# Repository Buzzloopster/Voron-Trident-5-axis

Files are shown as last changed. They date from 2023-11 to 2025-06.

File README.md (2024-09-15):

# Voron-Trident-5-axis
This is an 5 axis modification of Voron Trident 250mm 

Printer parameters:

CoreXYAC

Axis X and Y travel limits +110mm and -110mm from rotary bed centre

Axis Z travel limits Z + 130mm and Z -45mm 

Axis A can swivel 110 degrees in both directions

Axis C can turn infinite 

You can find two different versions of the Z-axis mechanism

DIRECT DRIVE EXTRUDER with OMG extruder

and

BOWDEN DRIVE EXTRUDER mounted at the back of the printer

https://youtube.com/@loopster77?si=zdEiBNTgb2wkNzhc

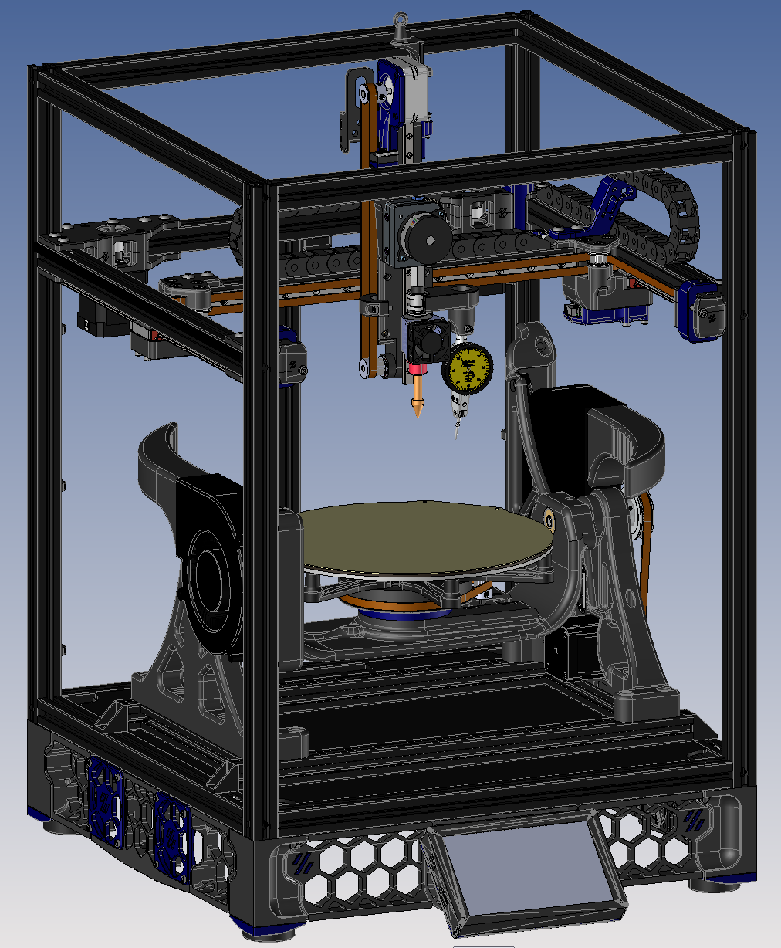
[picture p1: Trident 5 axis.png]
Trident 5 axis


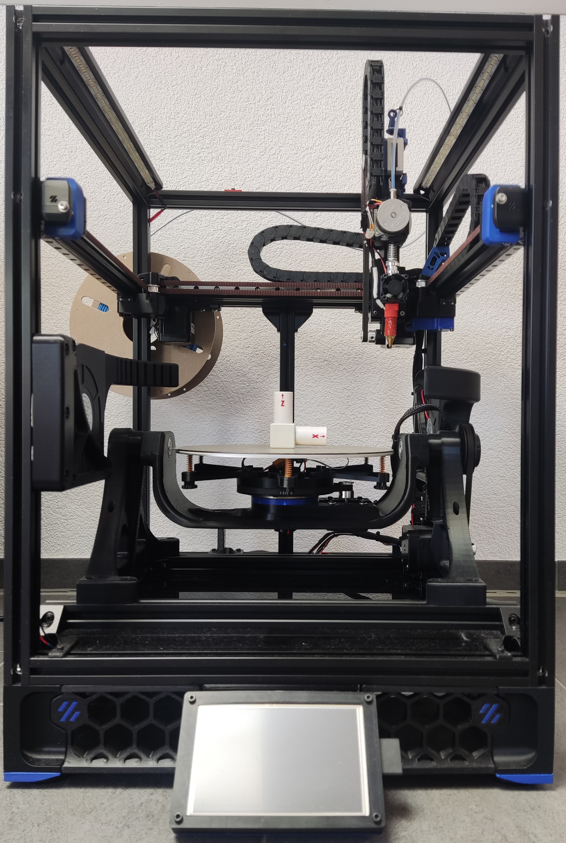
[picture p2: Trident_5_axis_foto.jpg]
Trident_ 5_axis_foto_1


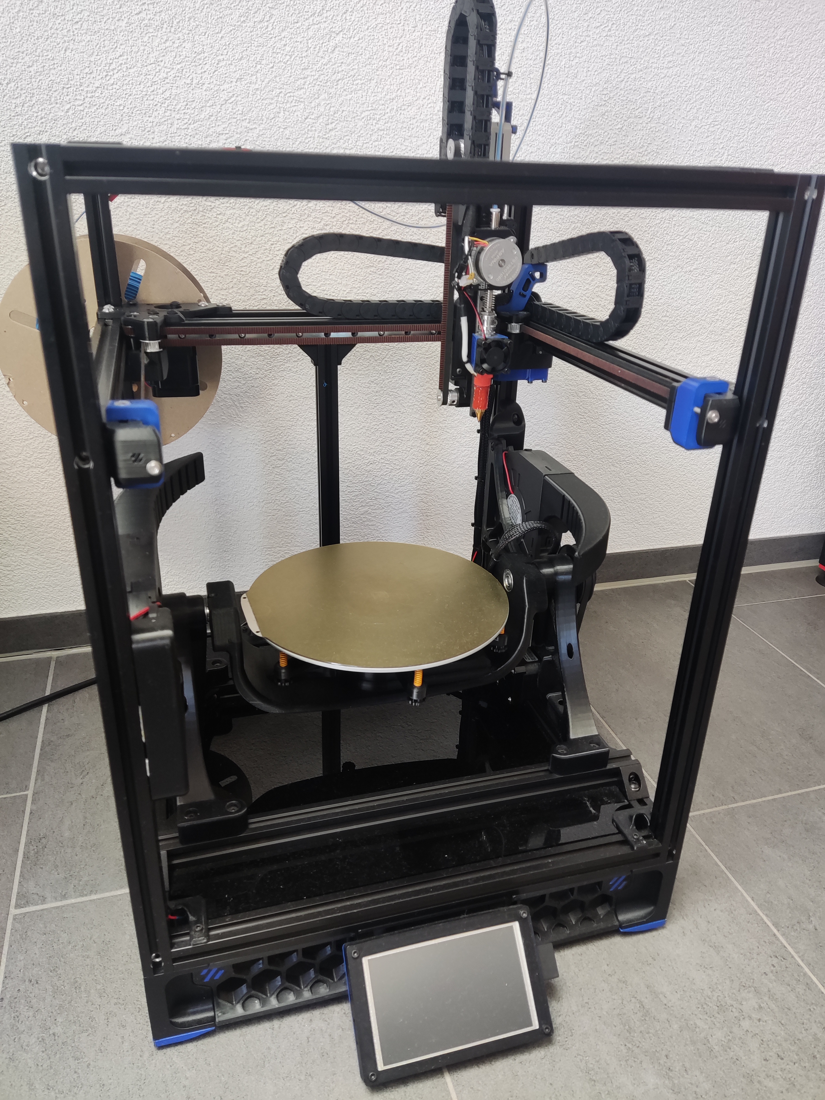
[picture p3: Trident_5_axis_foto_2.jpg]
Trident_ 5_axis_foto_2


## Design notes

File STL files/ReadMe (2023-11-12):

ALL PARTS ARE DESIGNED TO BE PRINTED WITH ABS FILAMENT! ! !

YOU CAN USE THIS SETTINGS FOR SLICING AND PRINTING THIS PARTS 

Layer height: 0.2mm
Extrusion width: 0.4mm, forced
Infill pecentage: 50%
Infill type:  gyroid, honeycomb, triangle, or cubic
Wall count: 5
Solid top/bottom layers: 5

NO WARPING!

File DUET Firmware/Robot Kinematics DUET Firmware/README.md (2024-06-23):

# RepRapFirmware_robot
only cpp, h and binaries

based on RRF 3.5.0beta3. To compile, use all related projects which are tagged with this release number.

Changes needed for compilation:
- Config/Pins.h add a SUPPORT_ROBOT flag and set to 1
- set other types to 0, for 6HC Hangprinter flag must be set (used for CAN)
- Kinematics.h change robot5axis to robot
- Kinematics.cpp add robot case to initiate the robot Kinematics class
- include RobotKinematics.* into Movement/Kinematics folder

The changed Pins.h, Kinematics.h and .cpp are checked in.

Duet 2 compilation is critical with memory usage, disable all other kinematics in Pins.h to have a chance.

For 6HC, the Hangprinter flag in Pins.h must be set.

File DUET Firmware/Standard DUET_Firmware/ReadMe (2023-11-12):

This is Firmware for Duet 6HC board with settings based on my build. 
For a new build the values of bed center needs to be recalibrated and adjusted to the absolute zero of printer

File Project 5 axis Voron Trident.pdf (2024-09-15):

## Project 5 axis 3D printer Voron Trident

For the project I chosed an 3D printer Voron Trident 250mm from open source, because of the excellent core XY gantry. The rotary bed and the Z axis extruder and hotend are designed as extention modules and can be adapted to any kind of core XY 3D printer. All parts are printed from ABS filament and in the future i would like to make the 3D printer fully enclosed.

Everything was its build, was considered for people on budget and with no access to CNC machines and whole build can be finished with a bit of knowledge of mechanics

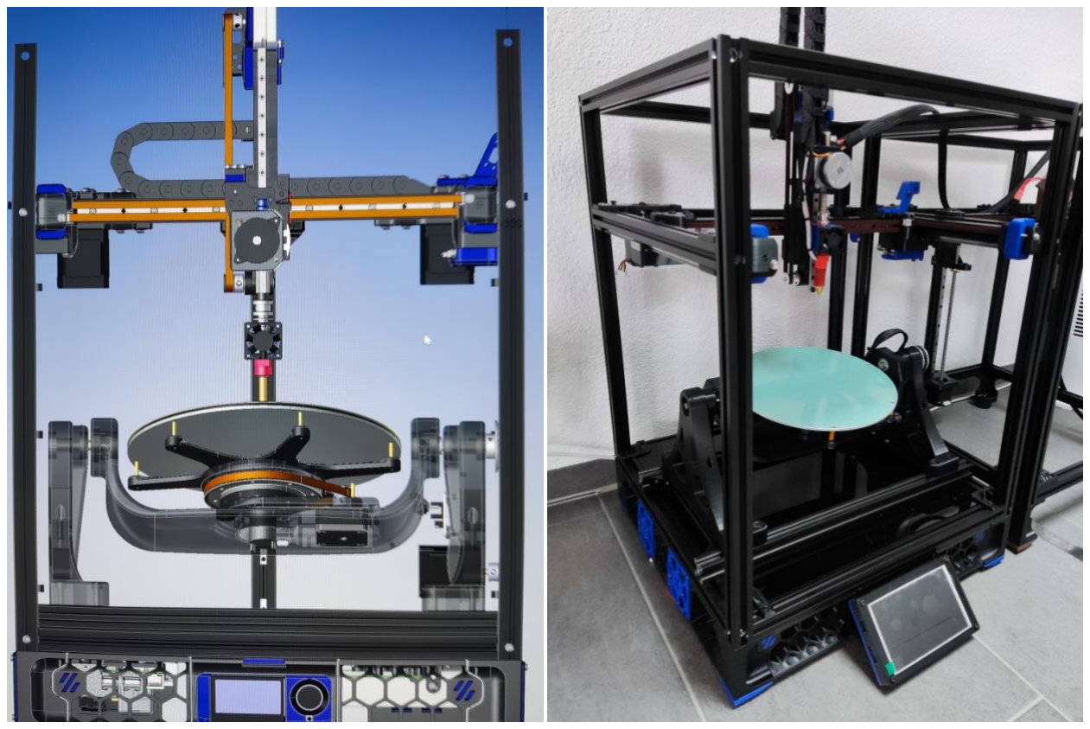
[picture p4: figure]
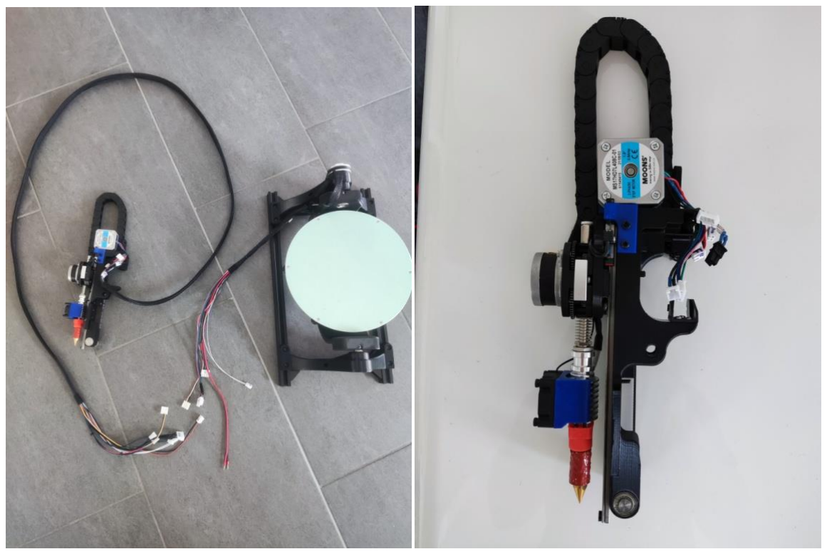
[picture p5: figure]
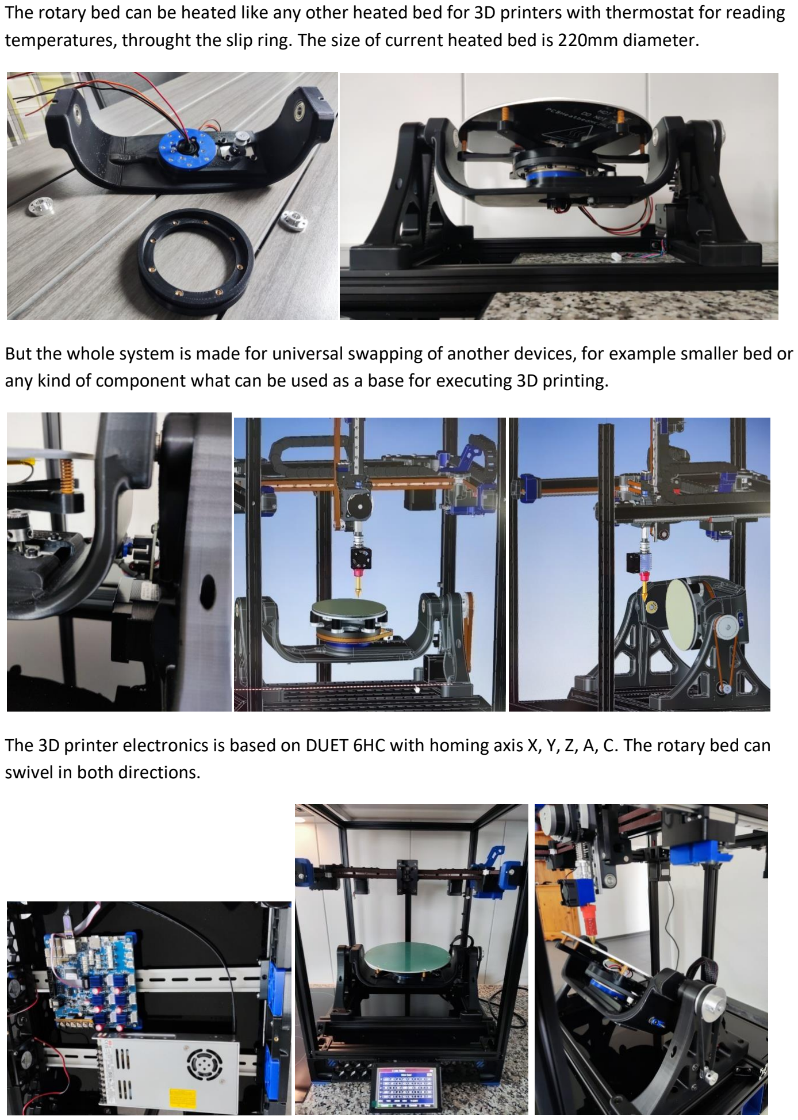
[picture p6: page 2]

The rotary bed can be heated like any other heated bed for 3D printers with thermostat for reading temperatures, throught the slip ring. The size of current heated bed is 220mm diameter.

But the whole system is made for universal swapping of another devices, for example smaller bed or any kind of component what can be used as a base for executing 3D printing.

The 3D printer electronics is based on DUET 6HC with homing axis X, Y, Z, A, C. The rotary bed can swivel in both directions.

The 3D printer is already build and tested only with standard slicers such as Prusa slicer or Super slicer. I have made indicator clock device to adjust the printer to the tight tolerances. The whole motivation behind this project is to bring and educate communities of hobbyists or people interested in additive manufacturing, new way of processing FDM methods to create and produce parts what can eliminate weak characteristics of layer adhesion by combining layer deposition from different angles of produced components.

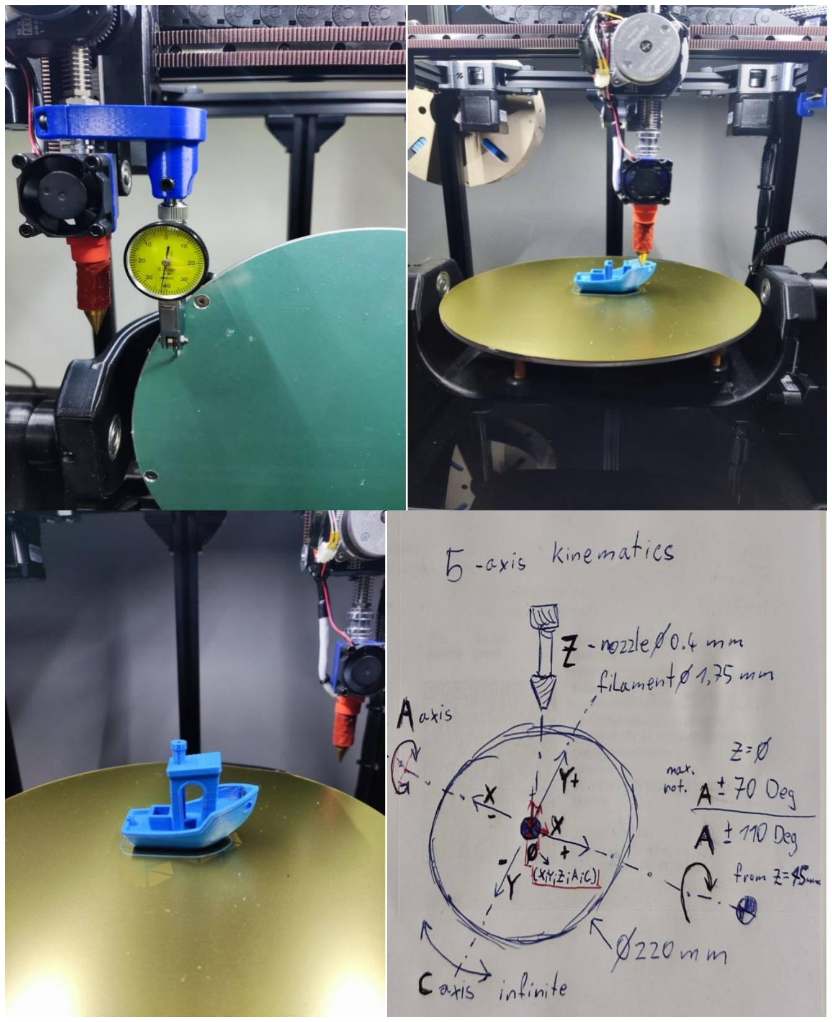
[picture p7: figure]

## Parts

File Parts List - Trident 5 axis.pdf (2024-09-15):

# Base

Aluminium Extrusion 2020 | Lenght 410mm | 2
Aluminium Extrusion 2020 | Lenght 180mm | 2
90 Degree corners | For Aluminium profile 2020 12
Screw | M5 x 10mm | 24
Screw | M5 x 20mm | 12
T nuts | M5 | 36
Heat insert | M3 x 5mm | 2
Screw SHCS | M3 x 8mm | 6
High precision Bearing | 608ZZ | 4
Spacer M8 x 1mm | | 2
Spacer M3 x 0.7 mm | | 4
Shaft 8mm Left | lenght 57 mm | 1
Shaft 8mm Right | lenght 79 mm | 1
Nema 17 stepper motor | 48mm 0.9deg, optimal 2.0Amp | 1

optical switch sensor for 3D

Closed loop GT2 belt 6mm | lenght 302 or 303 mm | 1
Pulley GT2 | 80 tooth 8mm bore | 1
Pulley GT2 | 16 tooth 5mm bore | 1
printer | 1

https://www.amazon
.com/MakerHawk-Optical-Endstop-Photoelectric-Control/dp/B07PMW
2QMT/ref=sr_1_1?ke
ywords=Optical+Ends
top&qid=170015654
4&sr=8-1

# Parts list Voron Trident 5-axis

# Table

Heat insert | M3 x 5mm | 52
Screw SHCS | M3 x 8mm | 52
Screw SHCS | M3 x 10mm | 20
Screw SHCS | M3 x 12mm | 1
Screw SHCS | M3 x 20mm | 6
Screw FHCS | M3 x 30mm | 6
Spacer M3 x 0.7 mm | | 7
NEMA_17_20mm 1.8deg | | 1
Pulley GT2 | 20 tooth 5mm bore | 1
Slip Ring | Dia 22mm 4CH 10A | 1

https://www.amazon
.com/s?k=slip+ring+4
+wire&crid=2COT7G
QJ0ZHZ7&sprefix=sli
p+ring+4+wire%2Cap
s%2C217&ref=nb_sb
_noss_1
IGUS ring | PRT_04_30
High precision Bearing | 608ZZ | 2
Closed loop GT2 belt 6mm | lenght 330mm | 1
Pololu Hub 8mm | The six M3 holes needs to be drilled with 3.2mm drill | 2
Round Heated bed round for kossel 220mm 24V | | 1
Round Magnetic sheet 220mm | | 1
Round PEI sheet 220mm | for kossel | 1
Bed spring | ID 3mm OD 6mm Lenght 15mm | 6
Diameter 90mm | 1

https://www.igus.ch/
product/iglidur_PRT_
04?artnr=PRT-04-30

# Z - axis Hotend with Extruder plus touch screen and blower fan

Heat insert | M3 x 5mm | 27
Heat insert | M2 x 4mm | 13
Screw SHCS | M2 x 6mm | 17
Screw SHCS | M3 x 8mm | 18
Screw SHCS | M3 x 10mm | 6
Screw SHCS | M3 x 12mm | 6
Screw SHCS | M3 x 14mm | 8
Screw SHCS | M3 x 16mm | 3
Screw FHCS stainless steel !!! | M3 x 8mm | 4
Screw FHCS | M3 x 22mm | 2
Screw FHCS | M3 x 6mm | 6
Screw BHCS | M5 x 10mm | 8
Screw BHCS | M5 x 25mm | 5
T nuts | M5 | 5
Hex nut | M3 | 4
Spacer M5 x 1mm | | 1
Spacer M2 x 0.5 mm wide | to fit the mouting hole | 4
neodymium magnets | 6 x 3 mm | 4
Self taping Screw | M2 size for micro switch | 2

MGN7 - H Linear Rail | Lenght 200mm | 1
NEMA_17_20mm 1.8deg | can be used from the voron kit | 1
Small Shaft 5mm | Lenght 45mm | 1
Shaft Collar 5mm | | 1
High precision Bearing | 625 ZZ | 2
Pulley GT2 | 20 tooth 5mm bore | 2
GT2 belt 6mm | Lenght 500mm | 1
Micro switch for 3d printer | | 1
Nonplanar nozzle | 0.4mm | 1
24V Ceramic Heating Core | CHC | 1
Heat Break For 1.75mm Filament M6 | for V6 Hotend | 1
Chain link 10x11 | 0.5m | 1
PTFE Tube OD 4mm ID 2.5mm | 1.0 M then cut it tio required lenght | 1
PTFE Tube OD 4mm ID 2.0mm | 200mm then cut it tio required length in between hot end and extruder | 1
24V Blower Fan 120x120x32mm | Printer will be installed with TWO Fans LEFT and RIGHT side | 2
24V Fan 30x30x10mm | | 1
Zip ties | | 100
Indicator Finger Clock for bed and axis calibration | 0.01mm sensitivity | 1

https://www.nonpla
nar.xyz/nozzles

https://imprimante-3dservice.com/gb/553-
trianglelab-chc-v6-
24v-115w-ceramicheater.html

https://en.wikipedia.
org/wiki/Indicator_(d
istance_amplifying_i
nstrument)

https://rdbarrett.co.uk/product/dial-test-indicatorhorizontal-type-08mm-001mm-mitutoyo-fingerclock/

## This parts are only for, if you decide to build Direct Drive version

DM1 OMG V2S Extruder kit with stepper motor and M6 to M10 adapter | with M6 to M10 adapter and stepper motor | 1
V6 HeatSink Extruder Radiator 3D Printer | bottom, top 1/8 or M10mm thread | 1

https://www.omgext
rd.com/productpage/omgextrd-omg-

https://store.dremc.com.a
u/products/omg-v2s-allmetal-direct-extruder-

# Z - axis Hotend with Extruder plus touch screen and blower fan

## This parts are only for, if you decide to build Bowden Drive version

PTFE Tube OD 4mm ID 2.0mm | 1M then cut it tio required length in between hot end and extruder | 1
V6 pro adapter in between nozzle and heat element CHC | M6 thread | 1
Phaetus x Voron Dragon Standard Flow or Highflow Hotend | | 1

https://meltbro.de/v
6-pro-adapterersetzt-volcanohotend-fuer-v6-
nozzle-duese-ausvernickeltem-

https://3do.eu/spareparts/672-v6-pro-adapterto-increase-super-flow-ofv6-rapidohot-end.html

https://www.3dmens
ionals.de/phaetus-xvoron-dragonhotend-st-2069#attr=9949,995
1,22290

https://www.phaetus.com
/products/phaetus-xvoron-hotend-st

Extruder for 1.75mm filament ( for exmple BondTech) mounted at back of the frame of the printer | BMG mounted with bracket on 2020 aluminium profile near to filamnet spool holder | 1
Pneumatic Coupler PC4-M10 With Collar | PC4 - M10 | 1

https://www.bondte
ch.se/product/bmgextruder/

https://www.whamb
amsystems.com/pro
ducts/metal-couplerpc4-m10

# Controls

Duet 6HC board | | 1
Power supply output 24V | 350W min. | 1
Paneldue touch screen 5" | | 1
Rj-45 cable, 0.5m | male to female | 1
Optional | Raspberry Pi4 | 1

https://www.duet3d.
com/duet3mainboar
d6hc

https://docs.duet3d.
com/Duet3D_hardwa
re/Accessories/Panel
Due

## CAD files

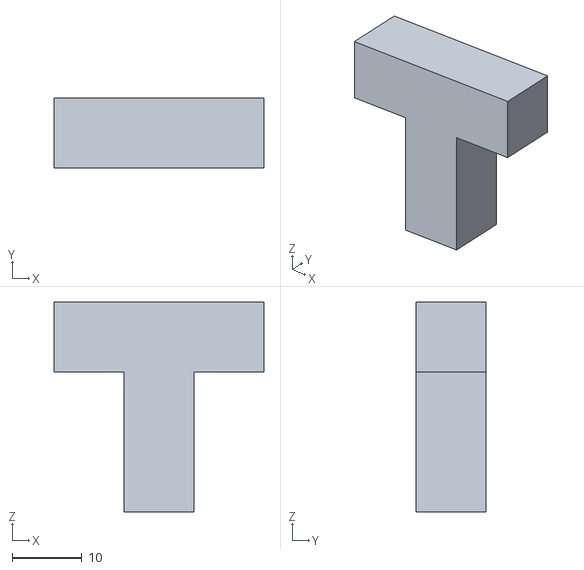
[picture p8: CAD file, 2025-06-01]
Printer Calibrations/T_letter.stl
30.0 x 10.0 x 30.0

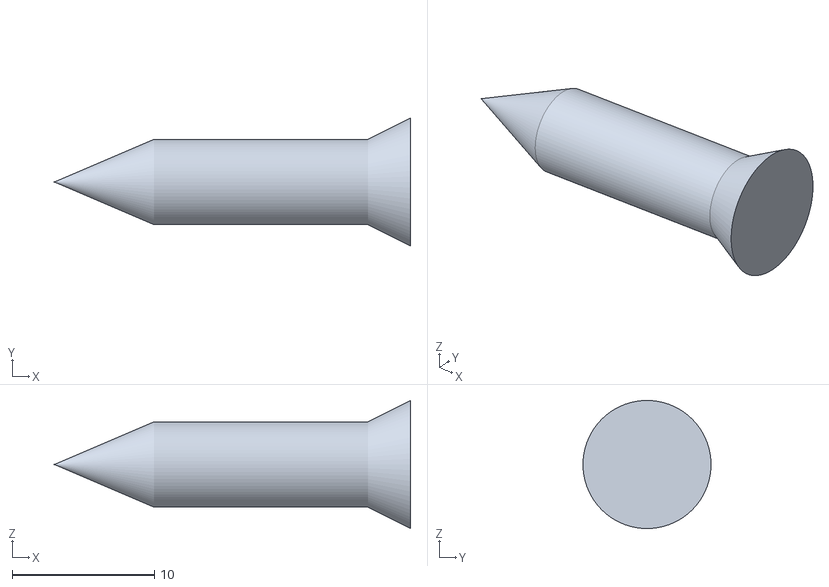
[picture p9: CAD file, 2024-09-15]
STL files/Robot Kinematics testing pin.stl
25.0 x 9.00 x 9.00

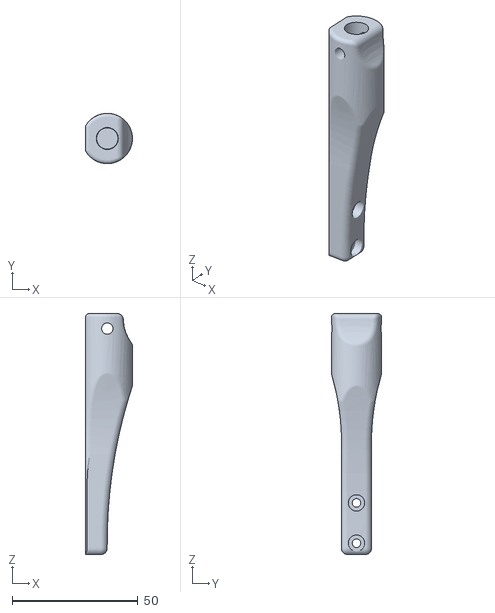
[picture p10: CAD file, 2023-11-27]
STL files/Z-axis Bowden drive - Dragon Hotend for Voron/indicator clock holder - Bowden drive.stl
18.7 x 20.0 x 95.8

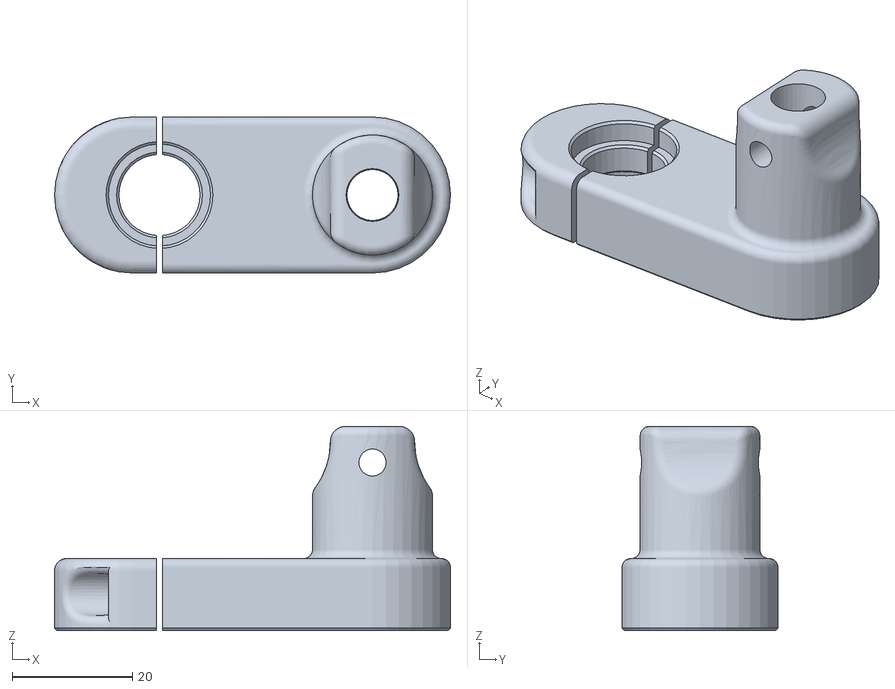
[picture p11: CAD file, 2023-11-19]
STL files/Z-axis Direct drive/indicator clock holder.stl
66.0 x 26.0 x 34.0

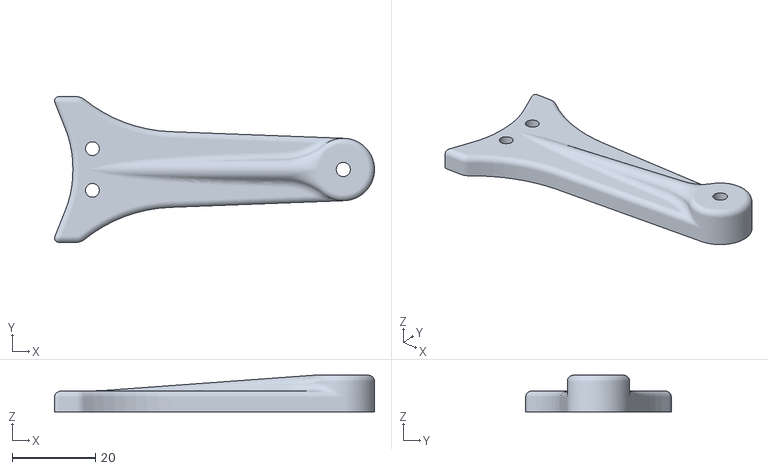
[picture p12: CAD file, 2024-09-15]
STL files/rotary table pivot ver 0.2.stl
76.9 x 35.0 x 8.80

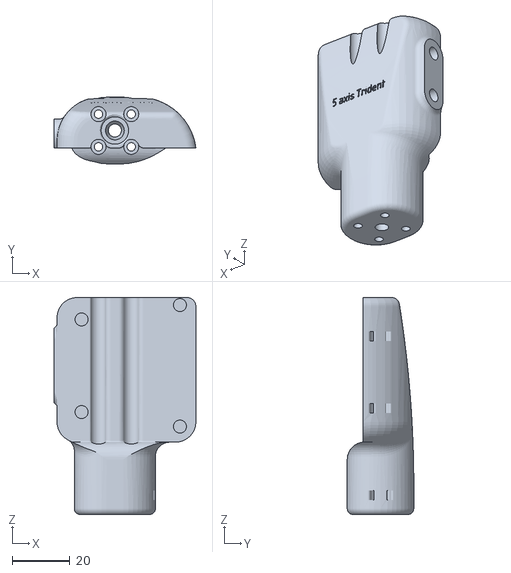
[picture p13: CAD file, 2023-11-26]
STL files/Z-axis Bowden drive - Dragon Hotend for Voron/Z-axis hotend holder.stl
49.0 x 23.0 x 75.0

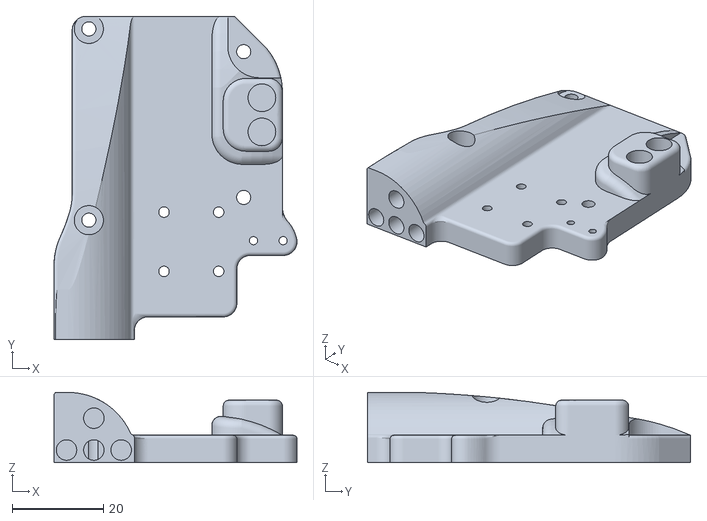
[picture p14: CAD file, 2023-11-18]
STL files/Z-axis Direct drive/Extruder_linerar_rail_mount.stl
53.4 x 71.0 x 15.4

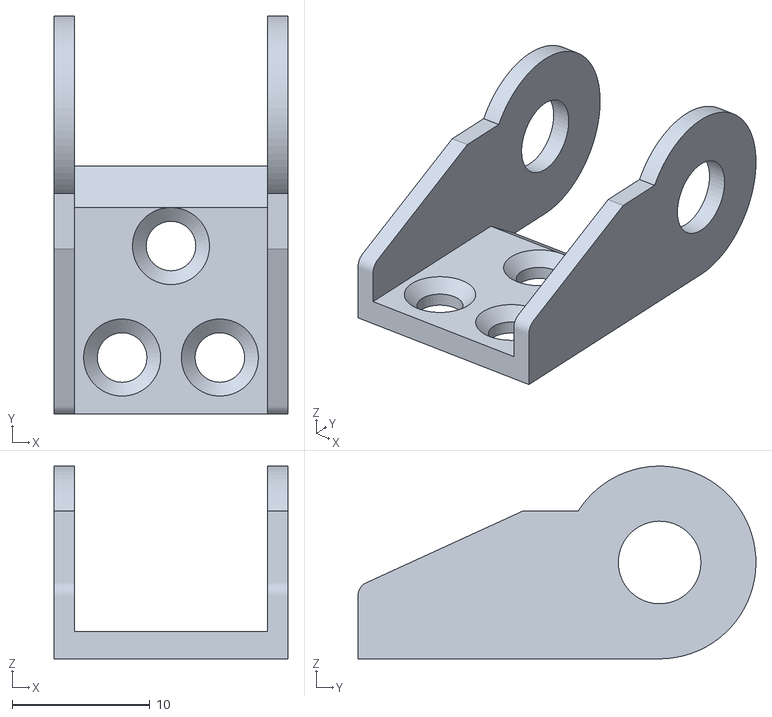
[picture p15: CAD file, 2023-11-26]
STL files/10x11-chain-edge2.stl
17.0 x 28.9 x 14.0

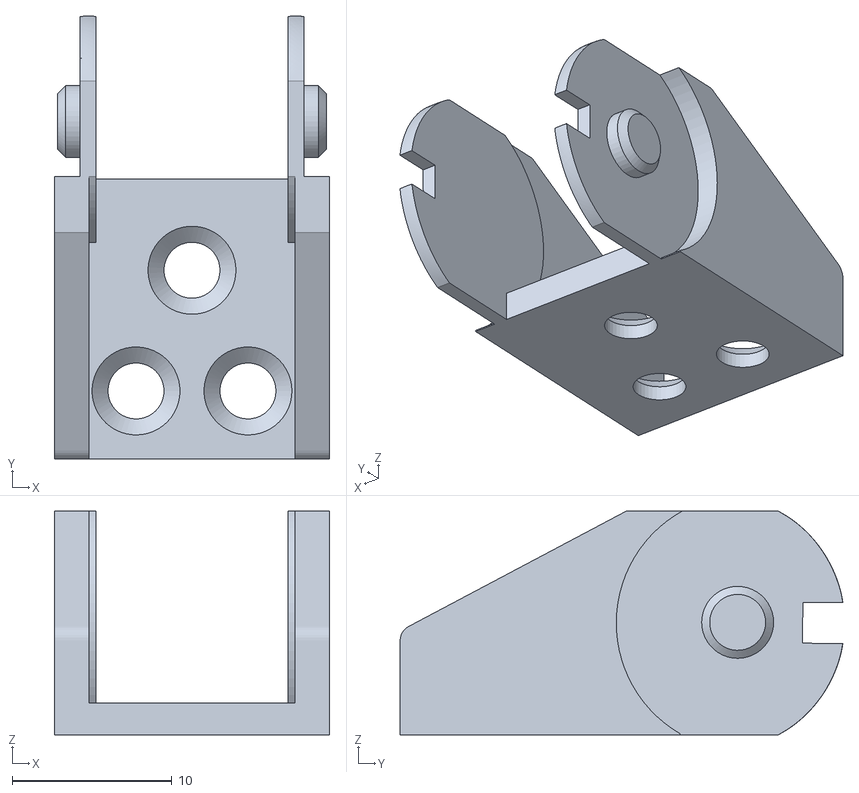
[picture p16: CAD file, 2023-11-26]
STL files/10x11-chain-edge1.stl
17.2 x 27.7 x 14.0

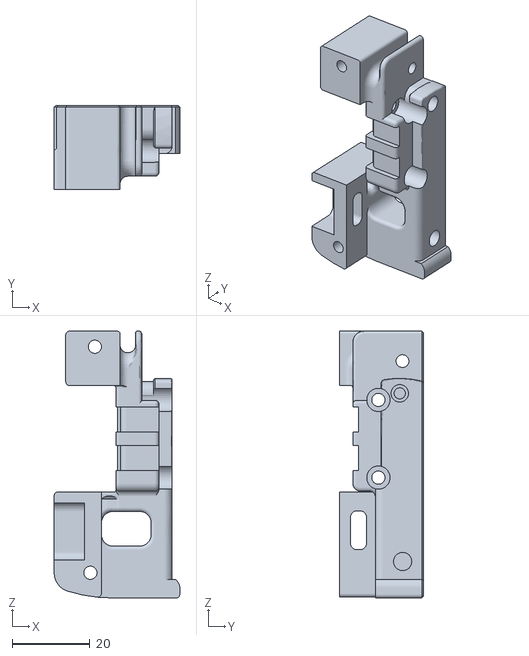
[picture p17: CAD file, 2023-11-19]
STL files/x_carriage_frame_right.stl
32.4 x 21.6 x 68.8

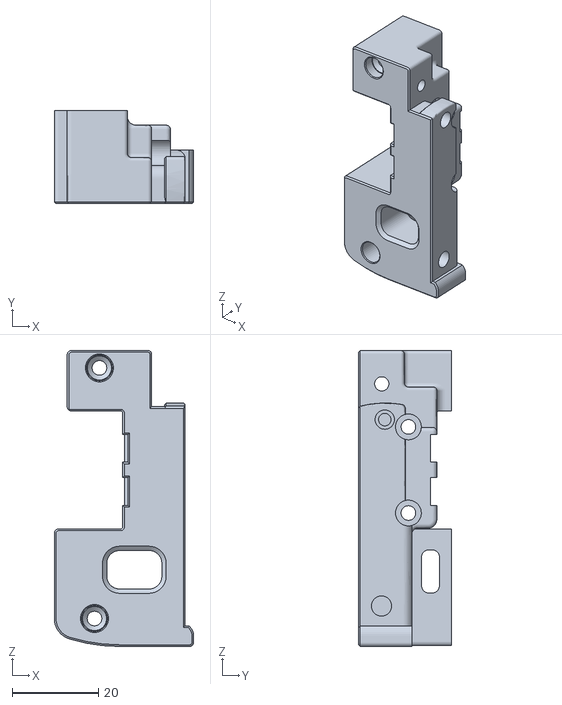
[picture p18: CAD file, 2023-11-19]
STL files/x_carriage_frame_left.stl
32.4 x 21.6 x 68.8

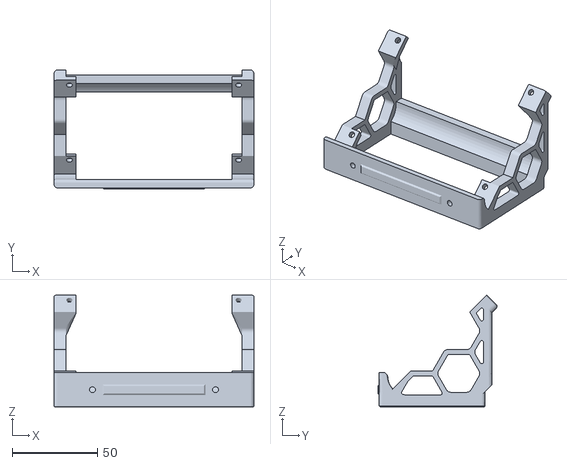
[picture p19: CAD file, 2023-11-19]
STL files/paneldue5_voron mount.stl
117.0 x 69.8 x 65.3

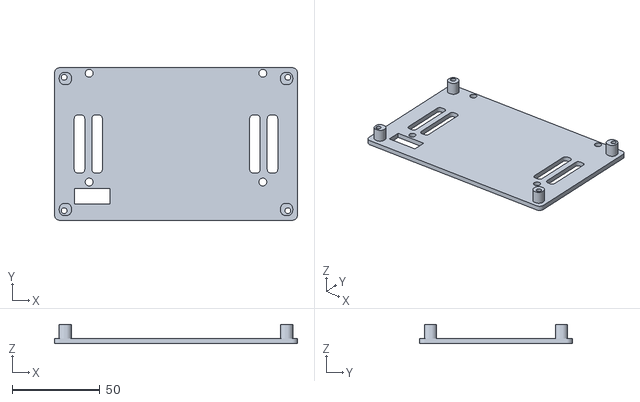
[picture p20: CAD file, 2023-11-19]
STL files/Paneldue5 rear mount.stl
138.5 x 87.0 x 10.8

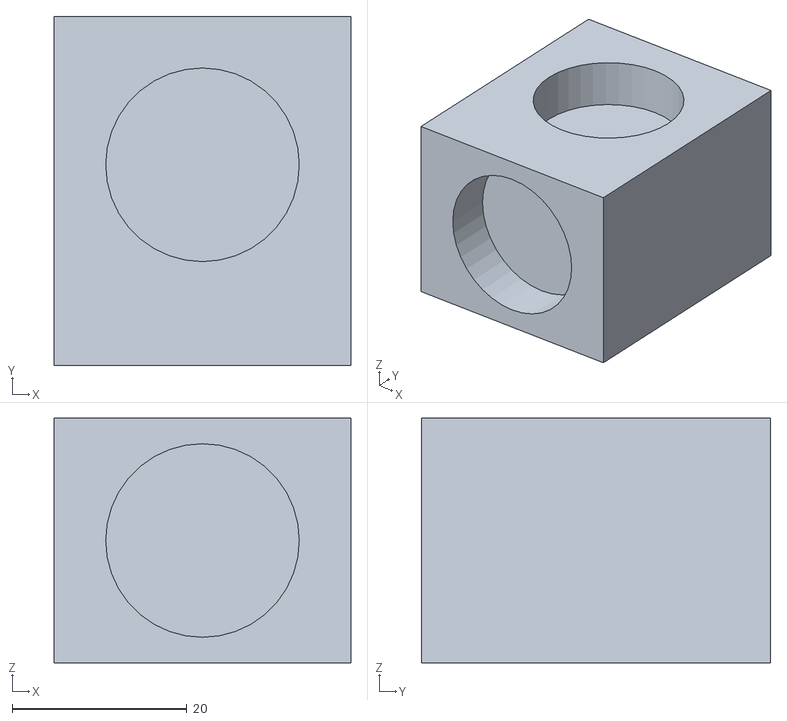
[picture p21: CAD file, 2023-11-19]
STL files/608ZZ bearing test.stl
34.0 x 40.0 x 28.0

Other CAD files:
STL files/Fan_Holder_2020_profile left.stl
STL files/VoronV0_CableManagementDuct.stl
STL files/paneldue_case_front.stl
STL files/Belt tensioner Top.stl
STL files/Belt tensioner.stl
STL files/Cooling Fan Holder.stl
STL files/Spacer_80mm.stl
STL files/Z endstop holder.stl
STL files/Z motor plate Nema 17.stl
STL files/endstop pin.stl
STL files/indicator clock holder grip.stl
STL files/rotary table gear wheel.stl

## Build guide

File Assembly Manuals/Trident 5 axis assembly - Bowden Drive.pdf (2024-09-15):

# Assembly Manual for Voron Trident 250mm

# 5 axis – Bowden Drive

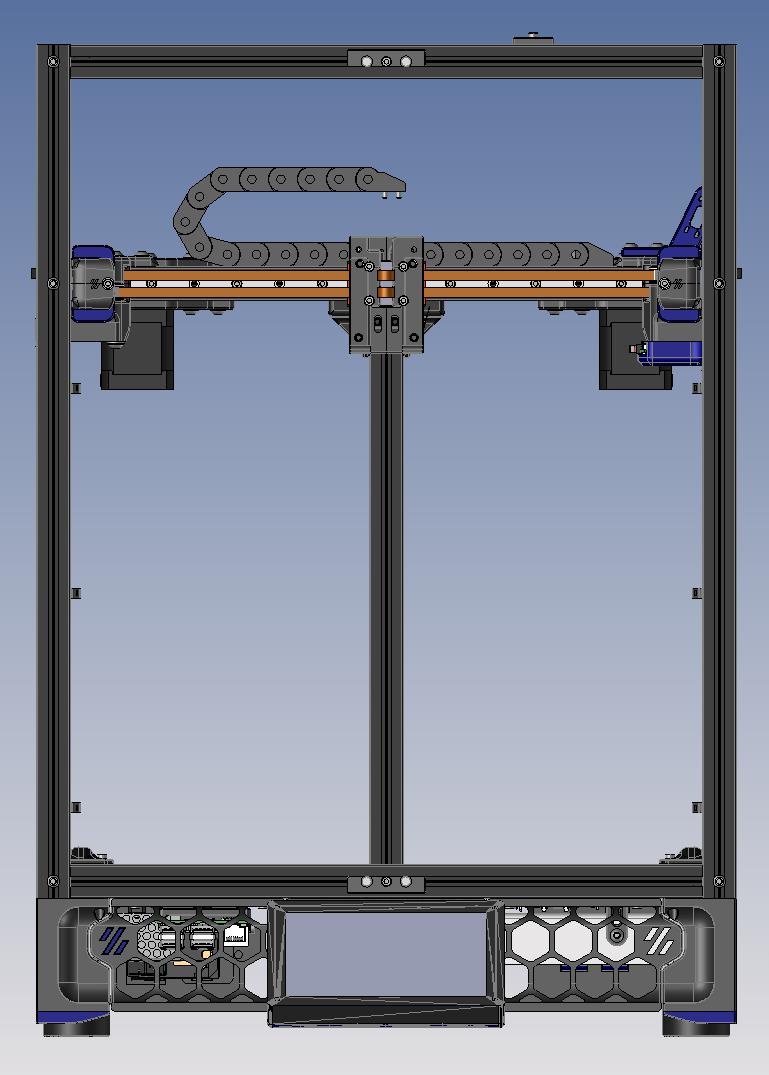
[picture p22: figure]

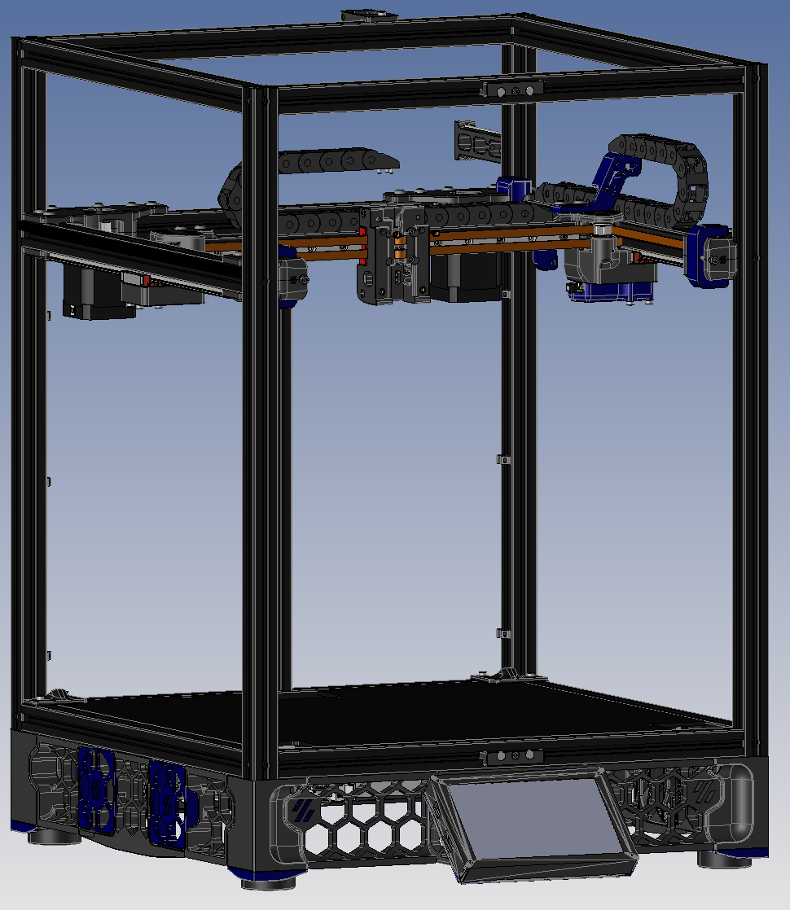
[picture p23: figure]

NOTE: From the Voron Trident kit 250mm you will need the complete frame, bottom skirts and

legs, complete core XY gantry and modified toolhead holder for extra two M3 heat inserts

control board is DUET 6HC with 24V Power Supply min. 350W

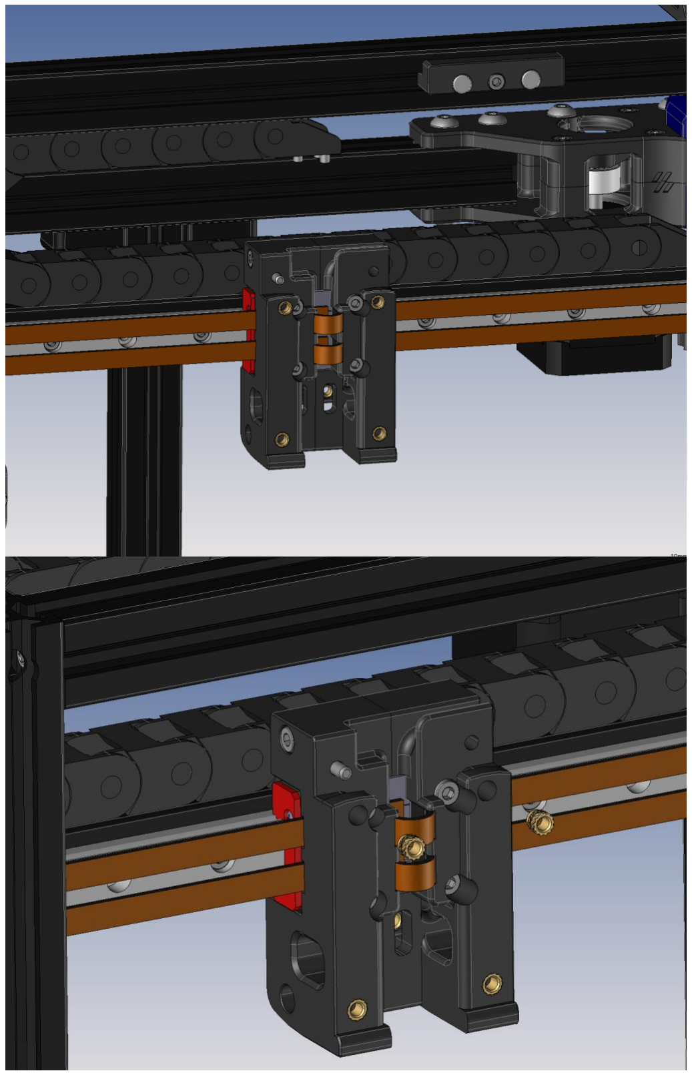
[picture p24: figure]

NOTE: the heat inserts used, are M3 x 5mm

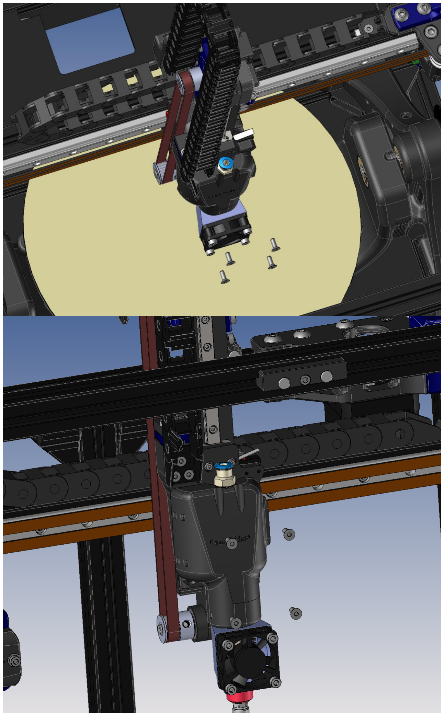
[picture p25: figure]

NOTE: | Screw FHSC M3 x 8mm Stainless Steel ! for magnets unnecessary
| interference

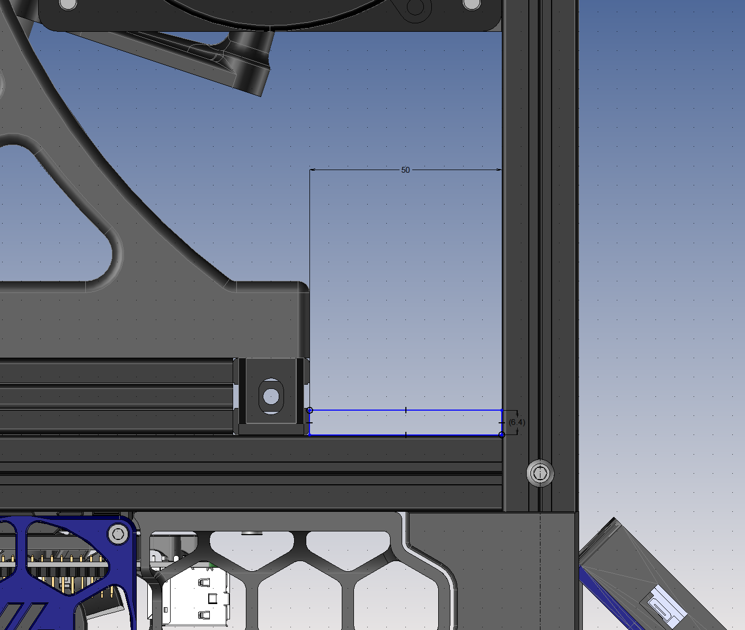
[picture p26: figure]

NOTE: Mount the A and C axis table 50mm from front frame

The calibration will be done later with indicator clock in calibrating steps

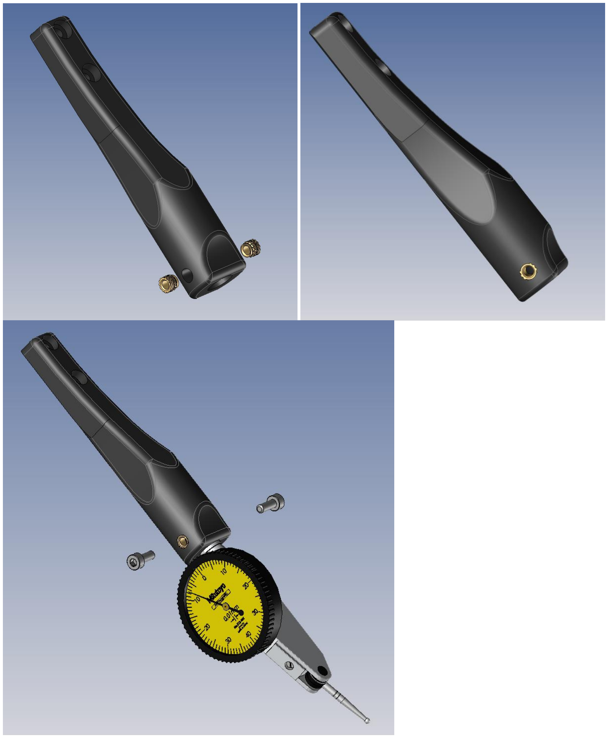
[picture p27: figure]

NOTE: heat inserts M3 x 5mm

Screw M3 x 10mm

Screw M3 x 8mm

NOTE: The indicator clock with holder are only needed, for calibration and check of axis

alignment

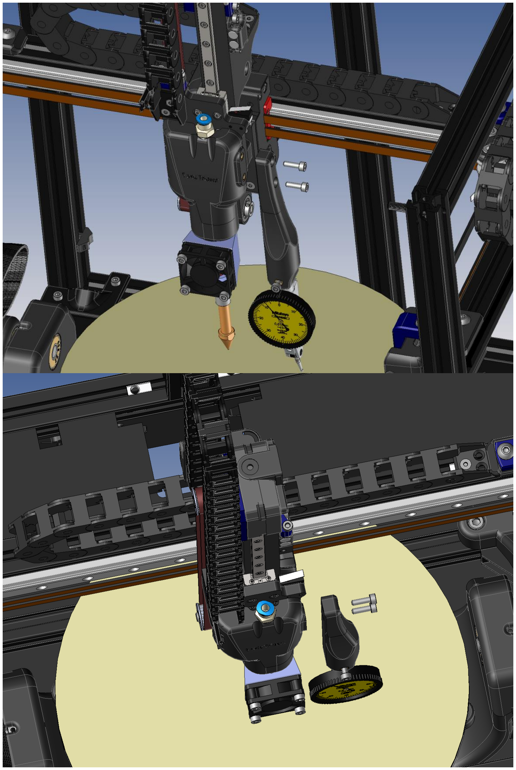
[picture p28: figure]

NOTE: Screw M3 x 10mm

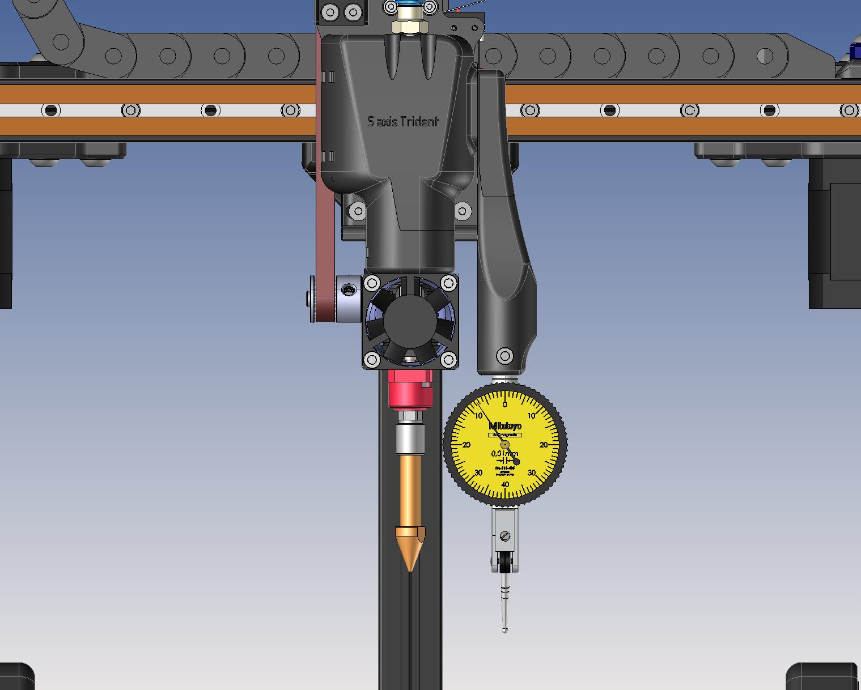
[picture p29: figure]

NOTE: For the Extruder please use type for 1.75mm filament and mount it on at back of the 2020

Of aluminium profile at the rear frame of the printer

You can use any extruder what is available on the market what you find and think its

suitable for the build.

Later on please calibrate the E steps of the extruder and update the value on DUET

mainboard

# Two Auxiliary Part fans Left and Right side

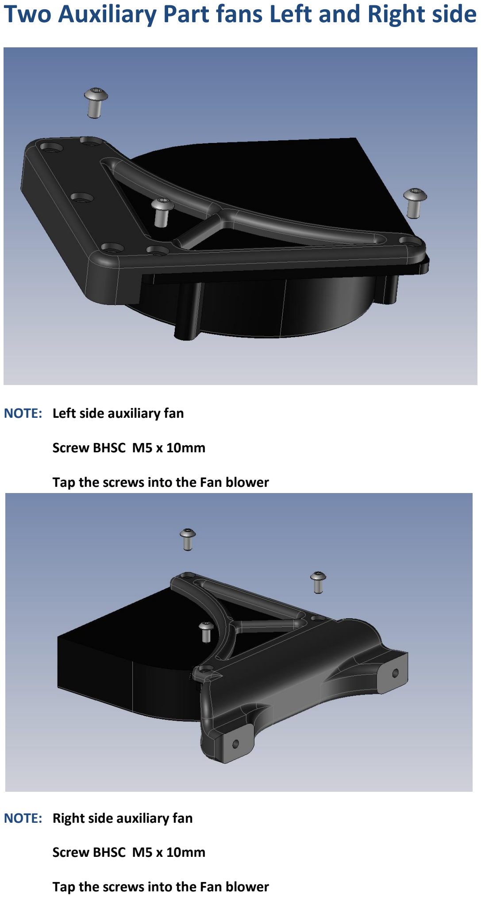
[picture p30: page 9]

NOTE: Left side auxiliary fan

Screw BHSC M5 x 10mm

Tap the screws into the Fan blower

NOTE: Right side auxiliary fan

Screw BHSC M5 x 10mm

Tap the screws into the Fan blower

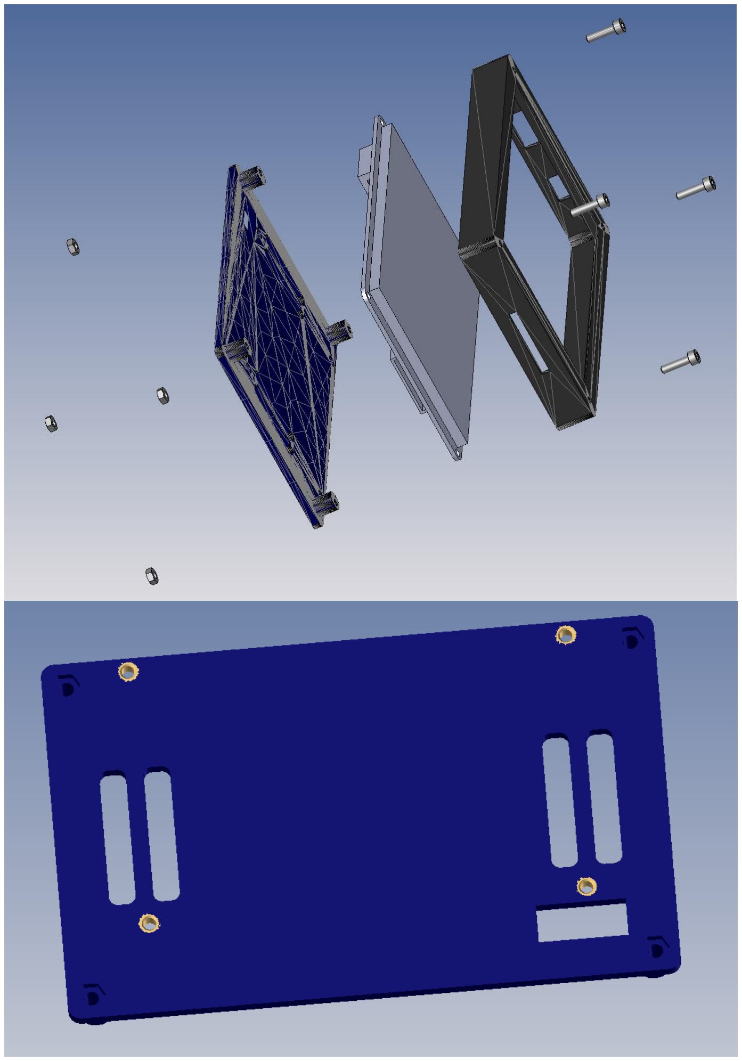
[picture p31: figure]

NOTE: heat inserts M3 x 5mm

Screw M3 x 12mm

Nut M3

Panel Due Touch screen 5”

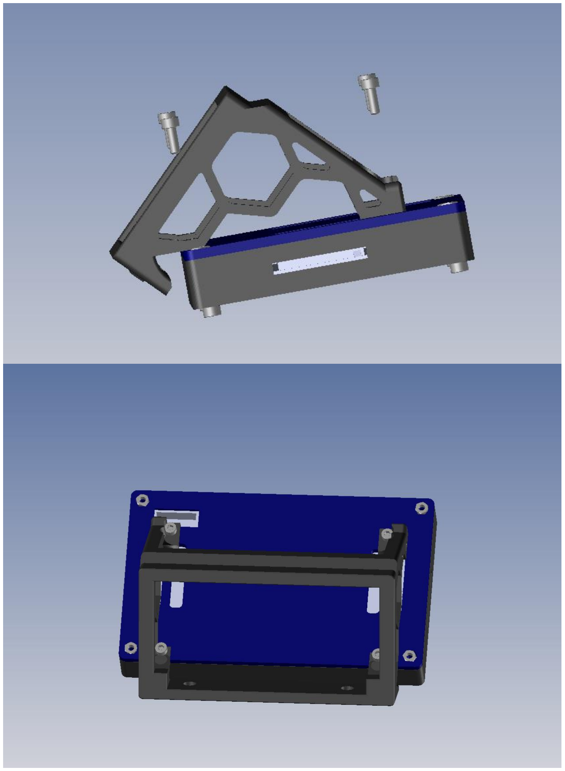
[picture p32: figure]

NOTE: Screw M3 x 8mm

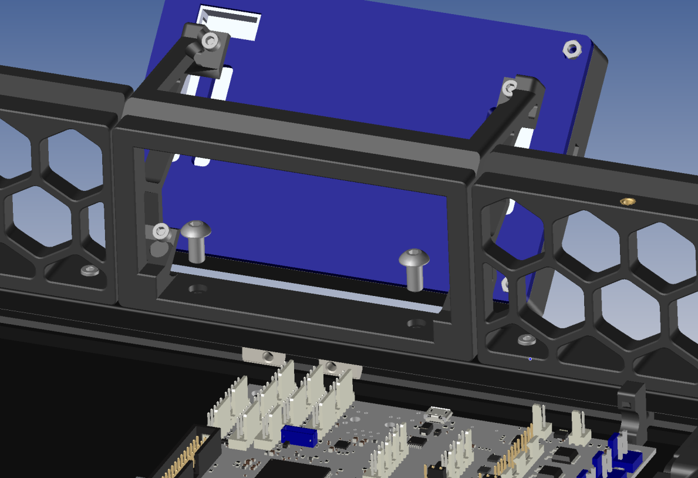
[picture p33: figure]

NOTE: Screw BHSC M5 x 10mm and T nuts

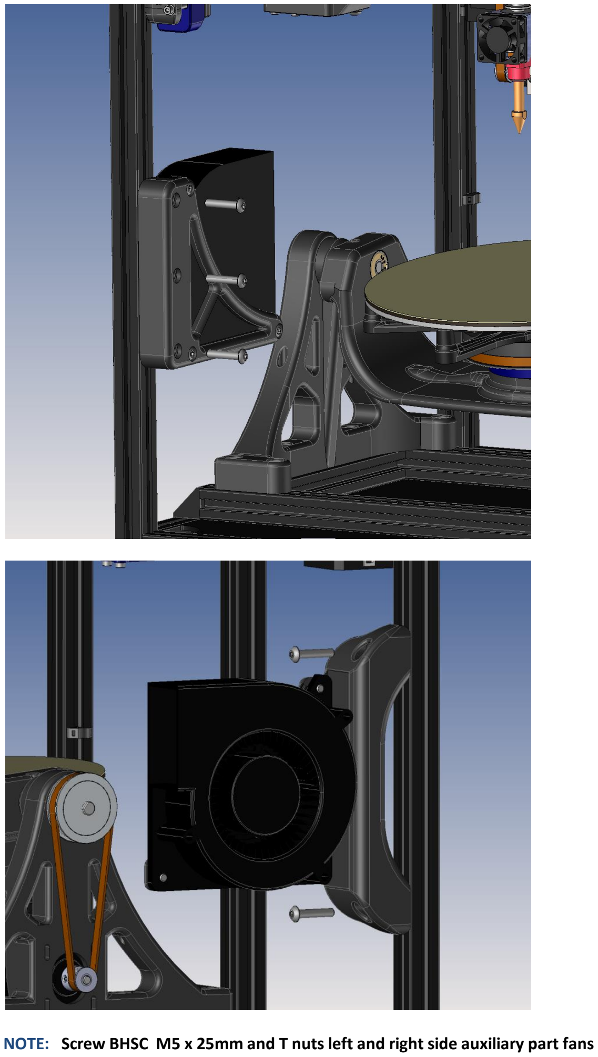
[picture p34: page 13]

NOTE: Screw BHSC M5 x 25mm and T nuts left and right side auxiliary part fans

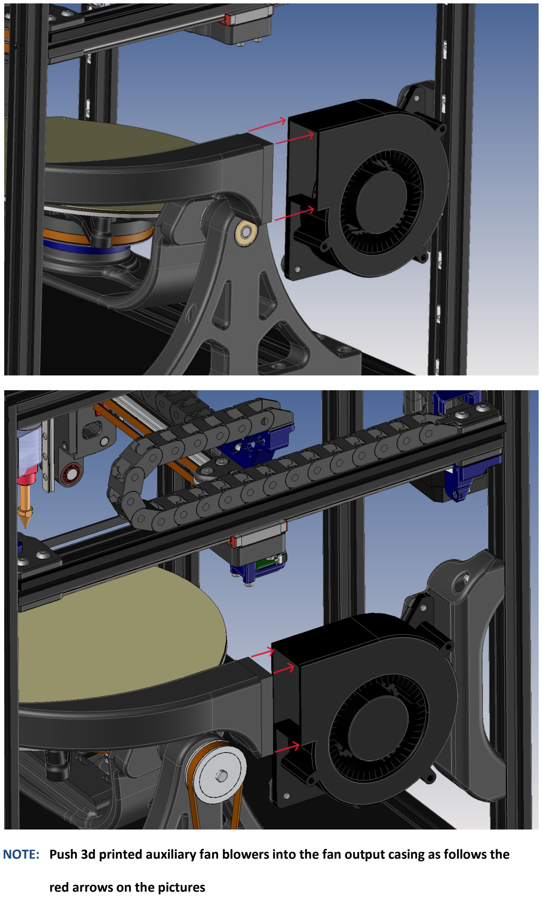
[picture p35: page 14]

NOTE: Push 3d printed auxiliary fan blowers into the fan output casing as follows the

red arrows on the pictures

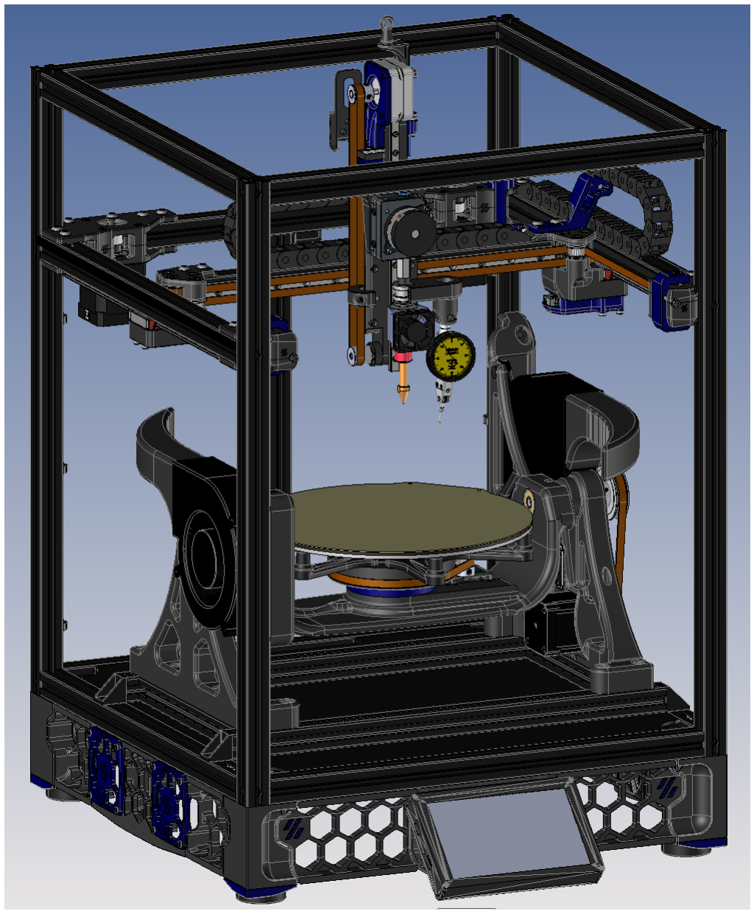
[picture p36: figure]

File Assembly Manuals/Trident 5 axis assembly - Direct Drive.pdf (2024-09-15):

# Assembly Manual for Voron Trident 250mm

# 5 axis – Direct Drive



NOTE: From the Voron Trident kit 250mm you will need the complete frame, bottom skirts and

legs, complete core XY gantry and modified toolhead holder for extra two M3 heat inserts

control board is DUET 6HC with 24V Power Supply min. 350W


NOTE: the heat inserts used, are M3 x 5mm

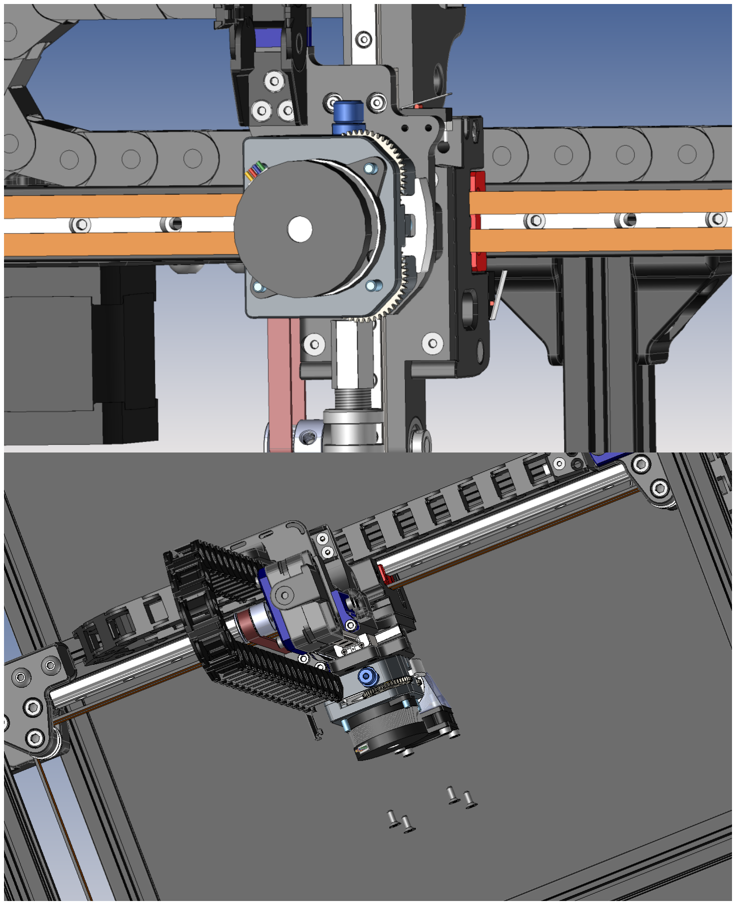
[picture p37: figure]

NOTE: | Screw FHSC M3 x 8mm Stainless Steel ! for magnets unnecessary interference

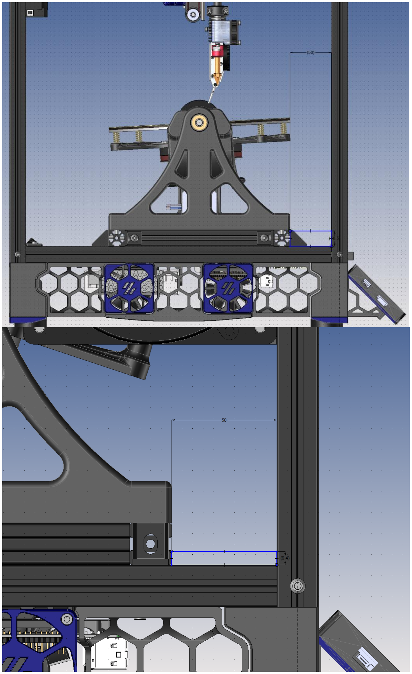
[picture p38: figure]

NOTE: Mount the A and C axis table 50mm from front frame

The calibration will be done later with indicator clock in calibrating steps

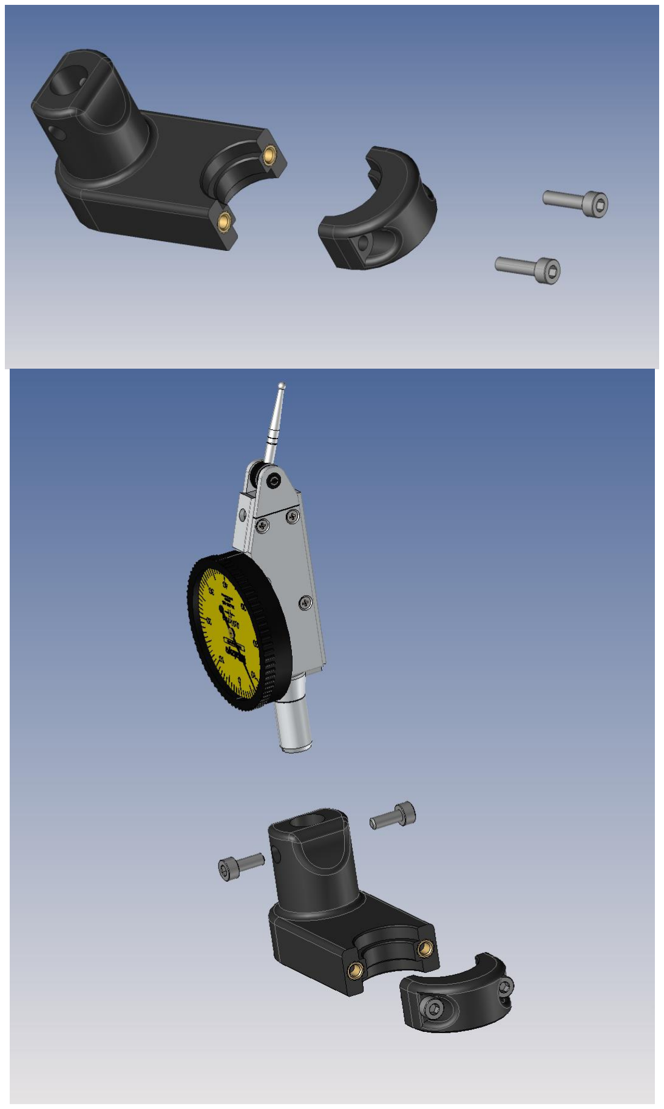
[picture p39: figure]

NOTE: heat inserts M3 x 5mm

Screw M3 x 12mm

Screw M3 x 8mm

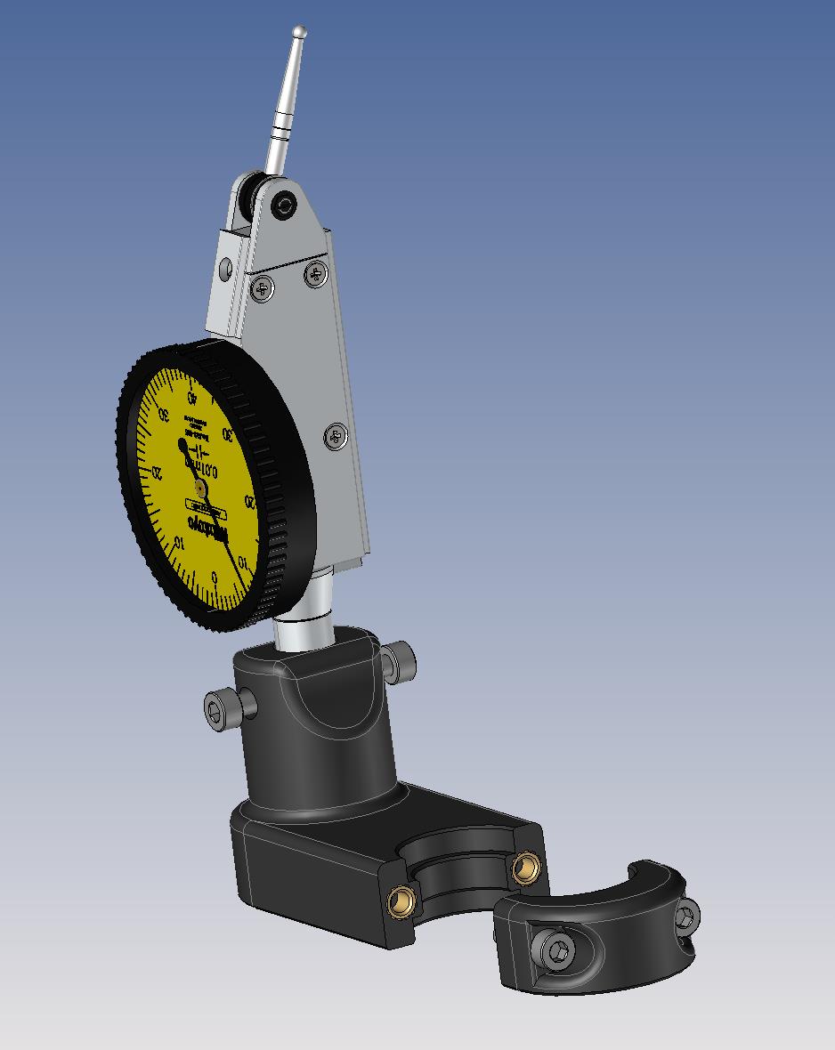
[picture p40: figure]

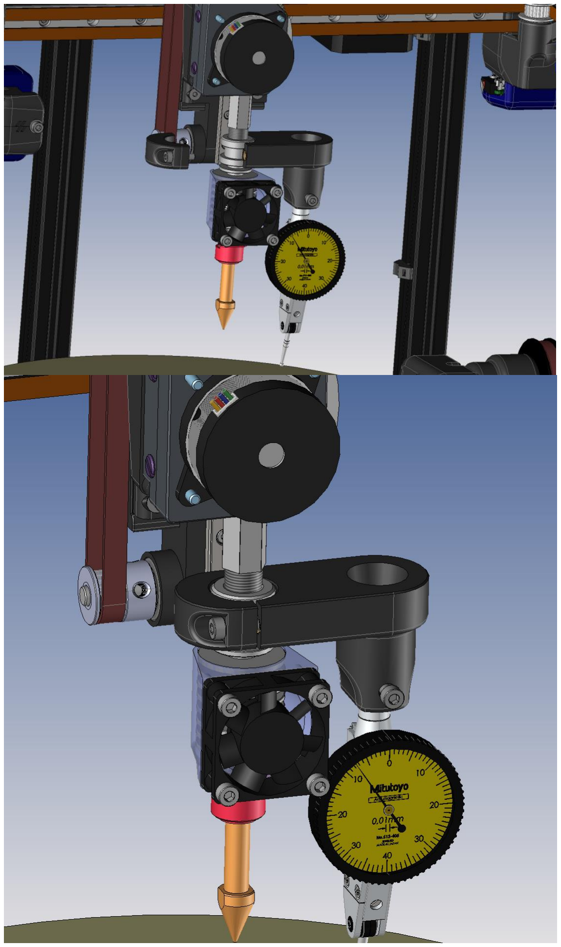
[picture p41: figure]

NOTE: The indicator clock and holder are only required for calibration and checking the axis Alignment.

## DO NOT PRINT WITH THIS ATTACHED TO THE HOTEND !

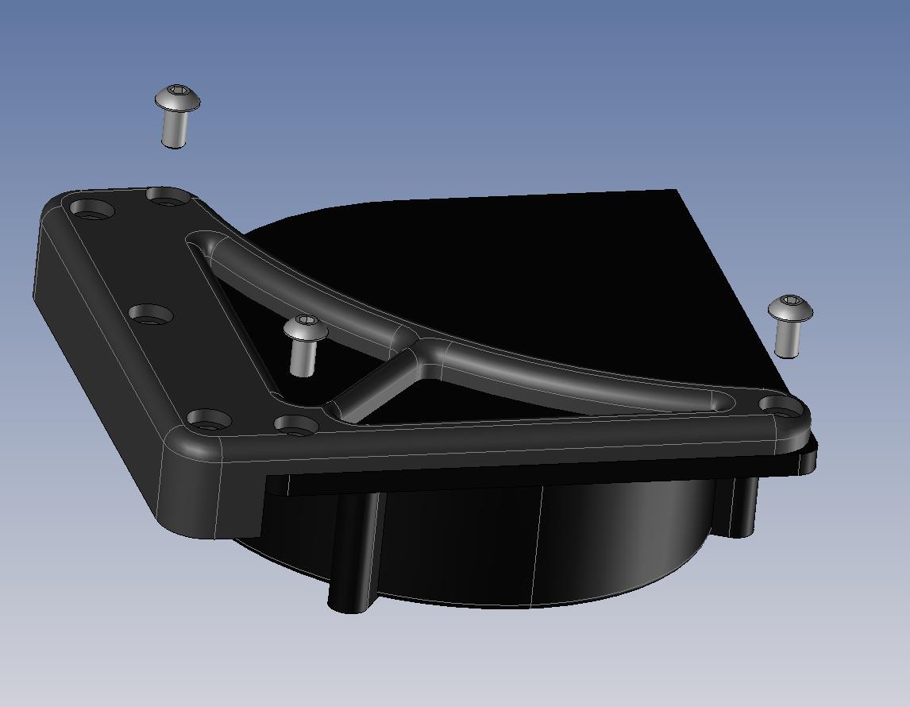
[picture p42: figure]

NOTE: Left auxiliary fan assembly

Screw BHSC M5 x 10mm

Tap the screws into the Fan blower

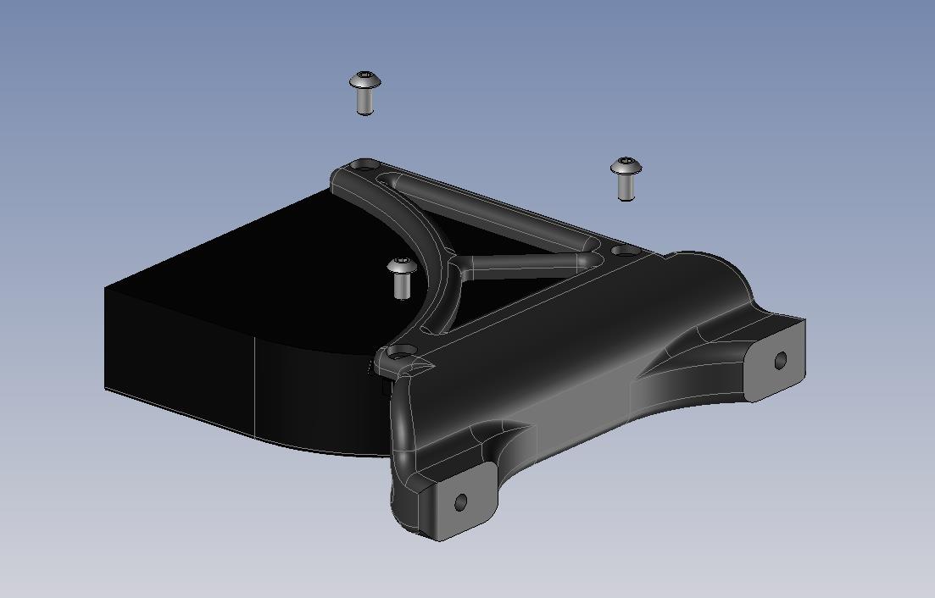
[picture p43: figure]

NOTE: Right auxiliary fan assembly

Screw BHSC M5 x 10mm

Tap the screws into the Fan blower

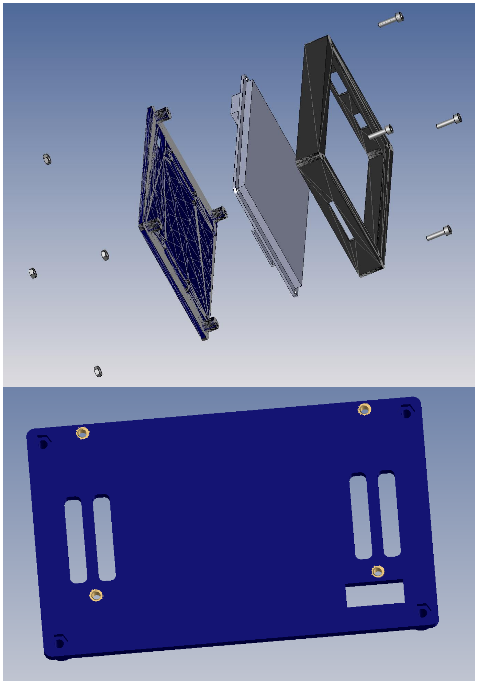
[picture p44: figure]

NOTE: heat inserts M3 x 5mm

Screw M3 x 12mm

Nut M3

Panel Due Touch screen 5”


NOTE: Screw M3 x 8mm

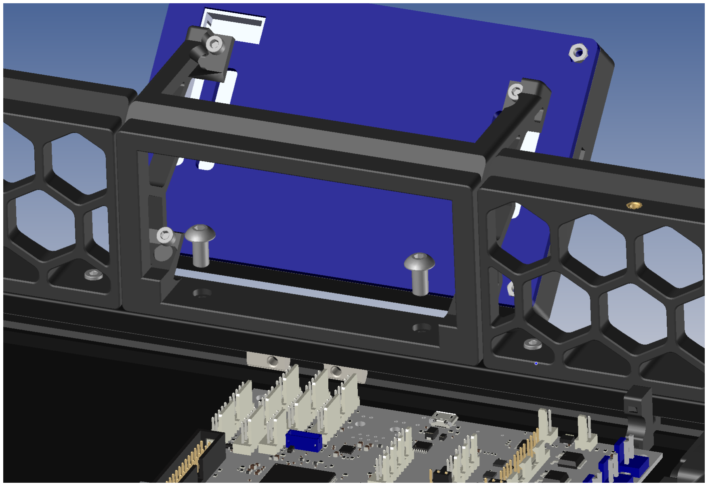
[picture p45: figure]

NOTE: Screw BHSC M5 x 10mm and T nuts

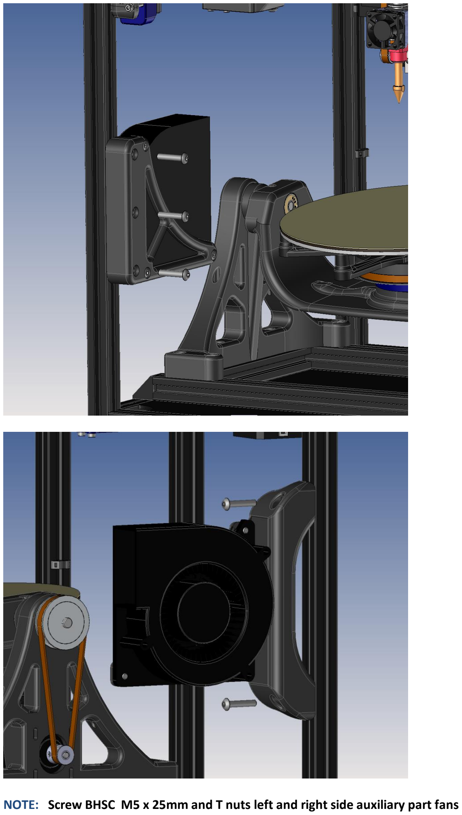
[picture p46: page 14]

NOTE: Screw BHSC M5 x 25mm and T nuts left and right side auxiliary part fans

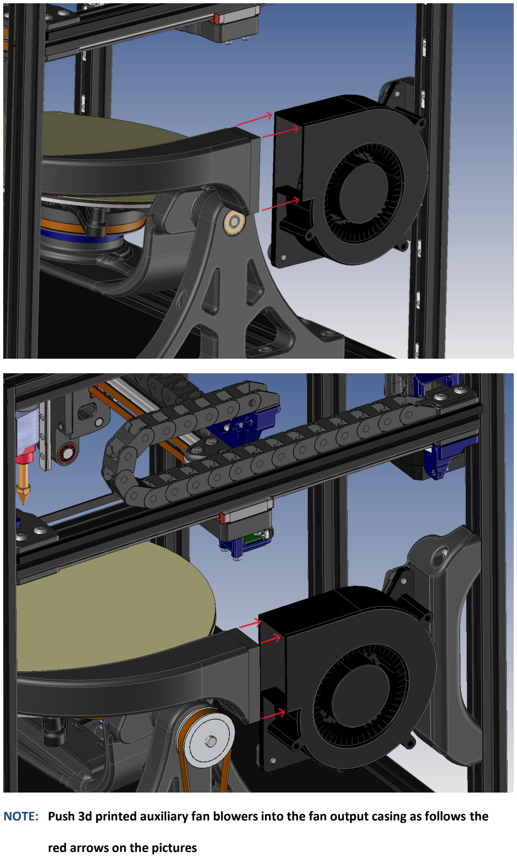
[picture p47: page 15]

NOTE: Push 3d printed auxiliary fan blowers into the fan output casing as follows the

red arrows on the pictures

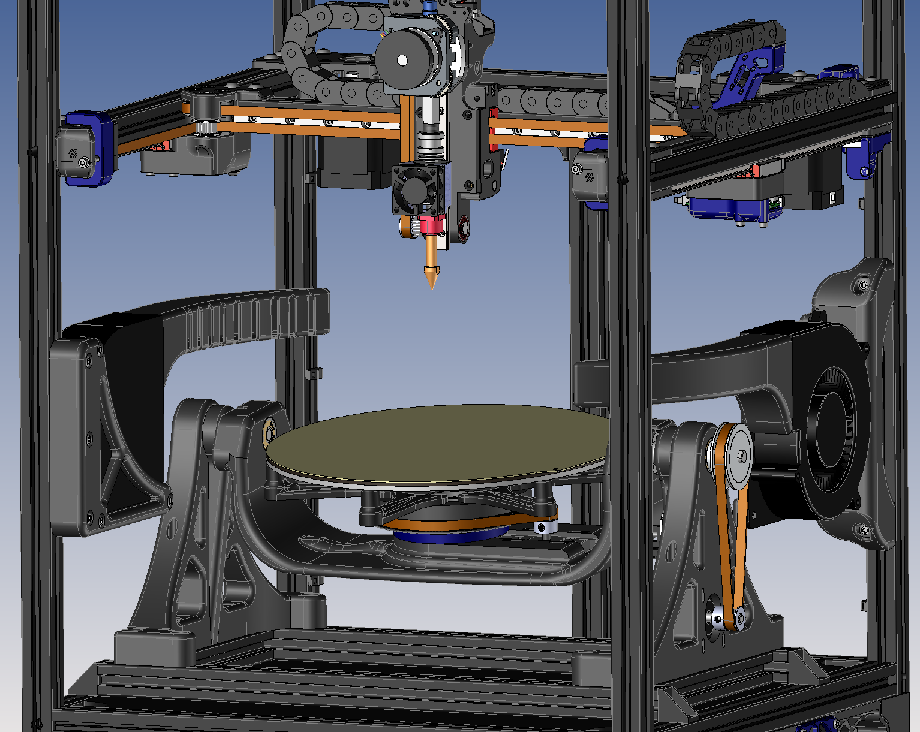
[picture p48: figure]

NOTE: Both auxiliary part fans after assembly

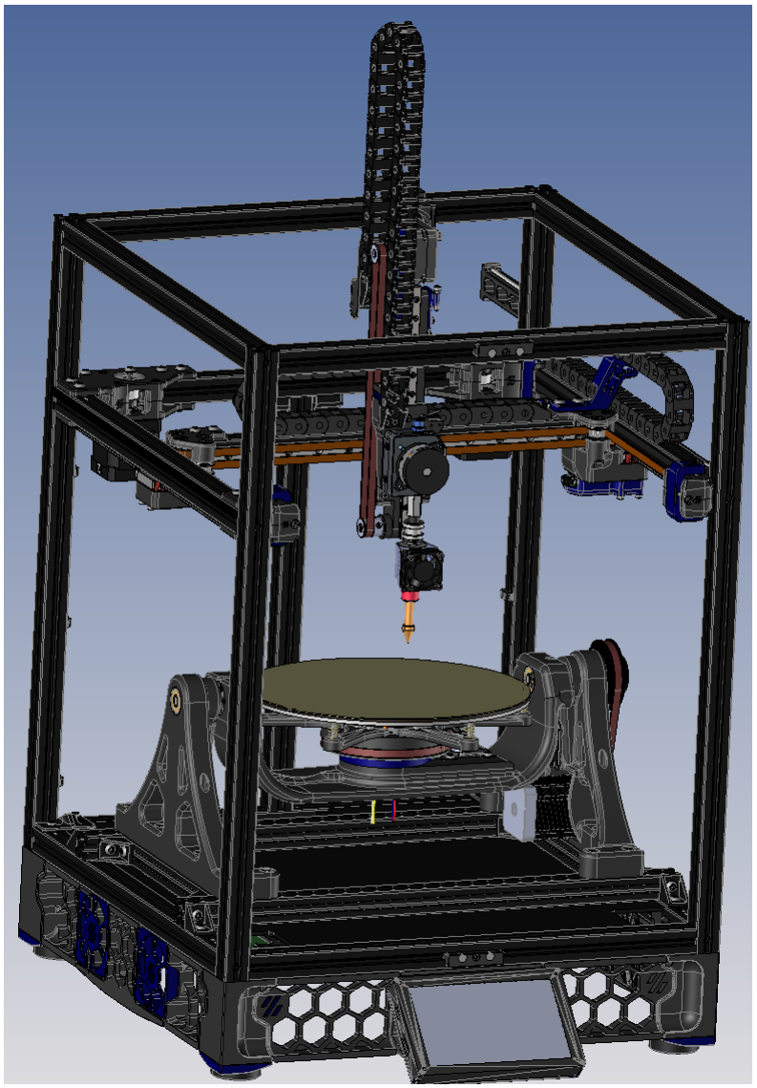
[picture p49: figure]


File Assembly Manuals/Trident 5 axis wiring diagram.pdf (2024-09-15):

# Wiring diagram Voron Trident 250mm

# 5 axis

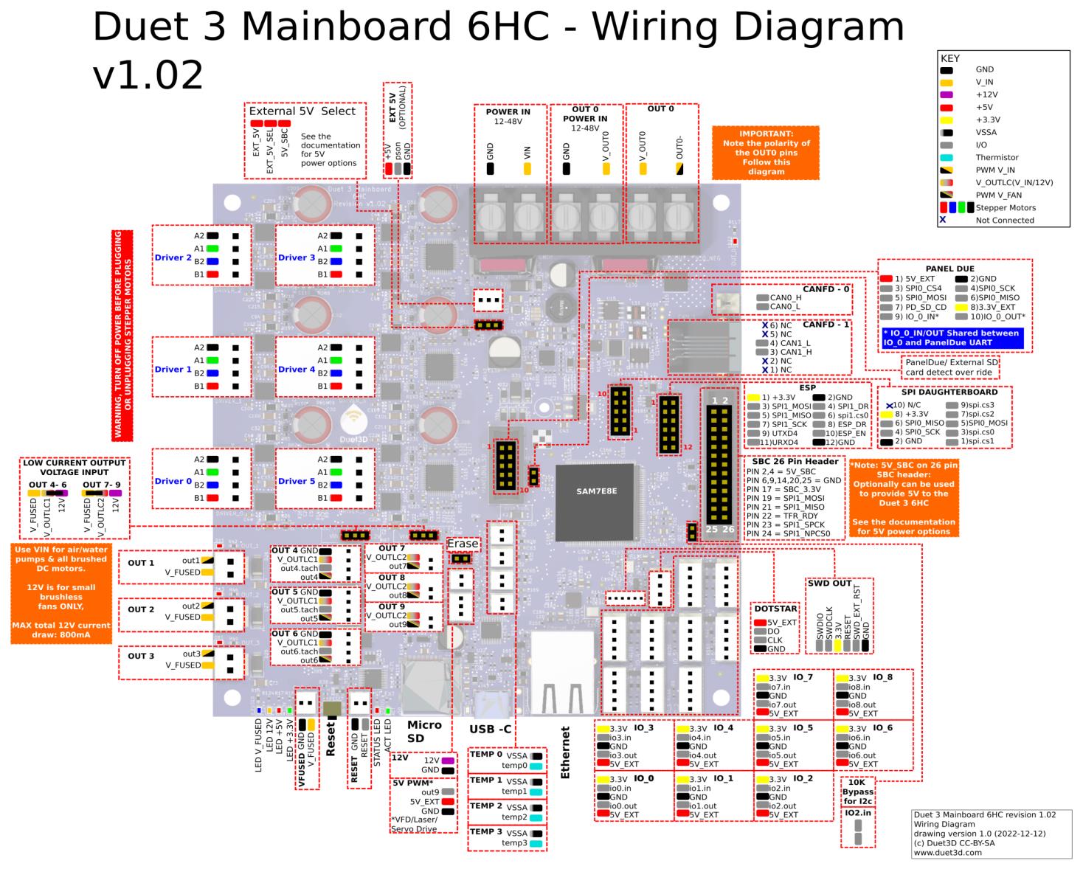
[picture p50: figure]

POWER IN | two wires (GND)- (VIN)+ | Power supply 24V
OUT 0 POWER IN | two wires (GND)- (V_OUT0)+ | Power supply 24V
OUT 0 | two wires (V_OUT0) + (OUT0)- | Rotary bed Aluminium heat bed
Driver 0 | four wires A2+A1+B2+B1 | Stepper motor X axis
Driver 1 | four wires A2+A1+B2+B1 | Stepper motor Y axis
Driver 2 | four wires A2+A1+B2+B1 | Stepper motor Z-axis
Driver 3 | four wires A2+A1+B2+B1 | Stepper motor extruder E
Driver 4 | four wires A2+A1+B2+B1 | Stepper motor A axis
Driver 5 | four wires A2+A1+B2+B1 | Stepper motor C axis
Temp 0 | two wires (VSSA) + (temp0) | Thermistor Bed
Temp 1 | two wires (VSSA) + (temp1) | Thermistor Hotend
IO_1 | three wires (io1.in)signal (GND)-(5V_EXT)+ | endstop X axis
IO_2 | one wire (io.2in) signal wire | endstop Y axis
IO_3 | two wires (io.3in)signal (GND)- | endstop Z axis
IO_4 | three wires (3.3v)+(io4.in)signal (GND)- | endstop A axis
OUT 1 | two wires (out1)+(V_FUSED) | Heat element on Hotend
OUT 4 | two wires (V_OUTLC1)+ (out4)- | 24V electronics cooling fan (side skirts)
OUT 5 | two wires (V_OUTLC1)+ (out5)- | 24V LEFT SIDE Blower radial fan for part cooling
OUT 6 | two wires (V_OUTLC1)+ (out6)- | 24V RIGHT SIDE Blower radial fan for part cooling
OUT 7 | two wires (V_OUTLC2)+ (out7)- | 24V 30x30x10 Hotend fan
OUT 8 | two wires (V_OUTLC2)+ (out8)- | 24V electronics cooling fan (side skirts)
OUT 9 | two wires (V_OUTLC2)+ (out9)- | 24V Led lights
PANEL DUE | Touch screen

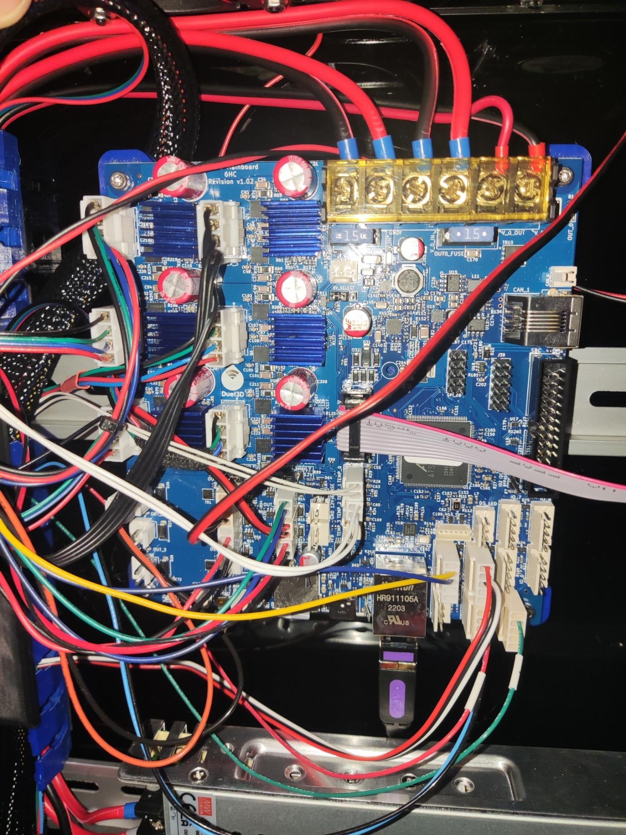
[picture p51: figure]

The connectors

The aluminium rotary bed connectors are for heating the bed i used XT-30 connector and for thermistor, JST connector. The thermistor is held with kaplon tape. Please keep the wires short so they will not interfere with components when the bed is rotating.

See more at the pictures below:

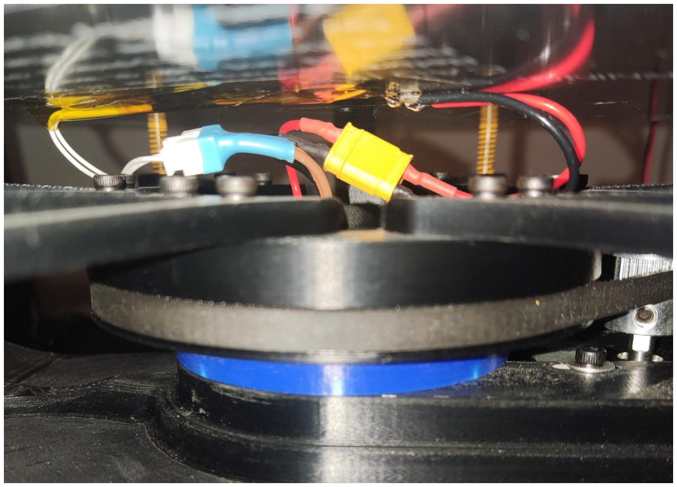
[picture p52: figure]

The wiring on the swivel bed is going through designed hole and continue with zip ties

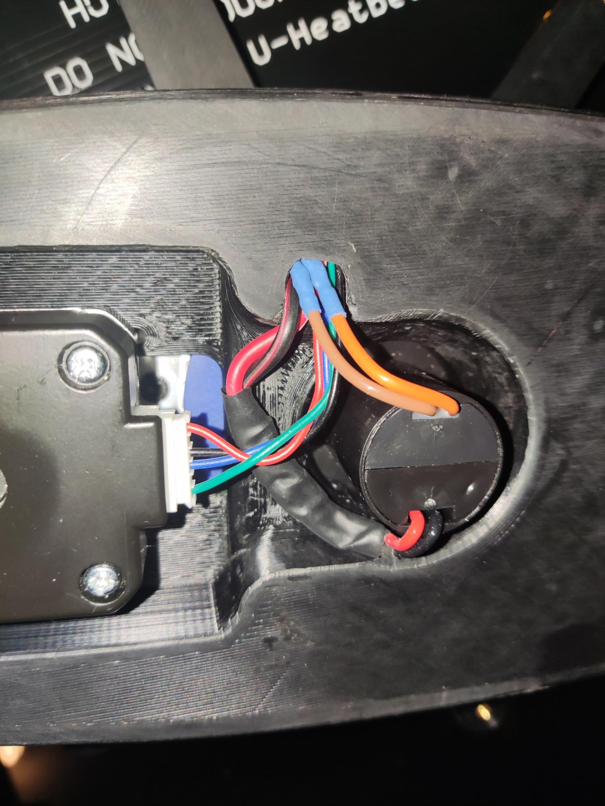
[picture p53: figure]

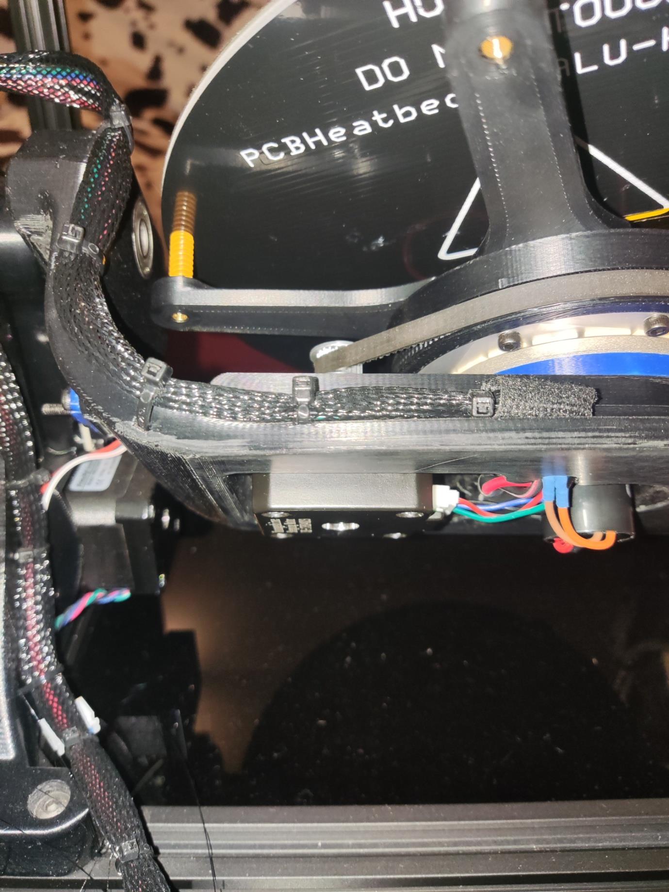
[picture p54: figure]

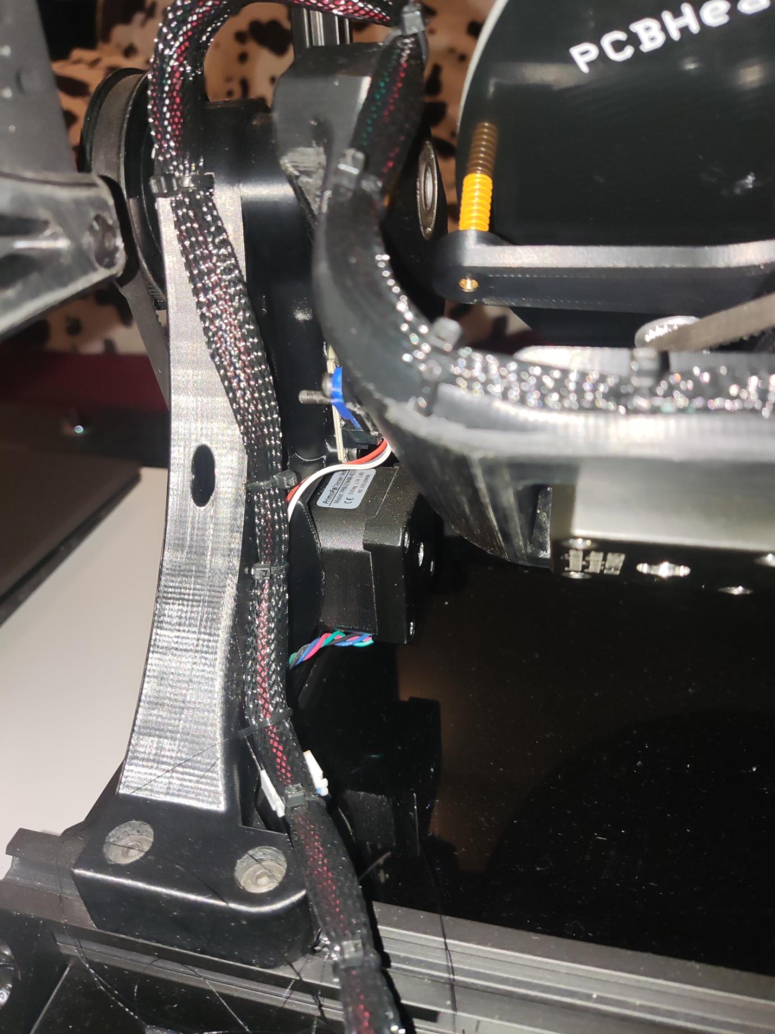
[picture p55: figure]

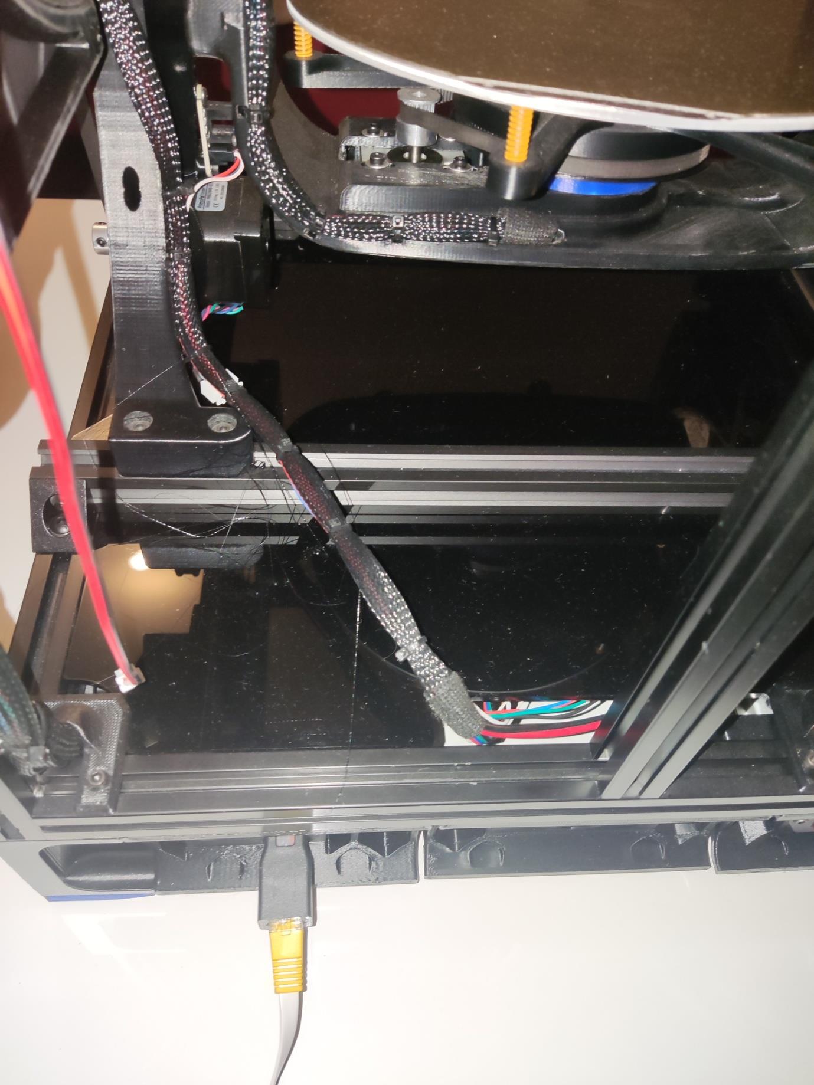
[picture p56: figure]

Please make the Hotend and thermistor wires with connectors so it can be dismounted when needed .

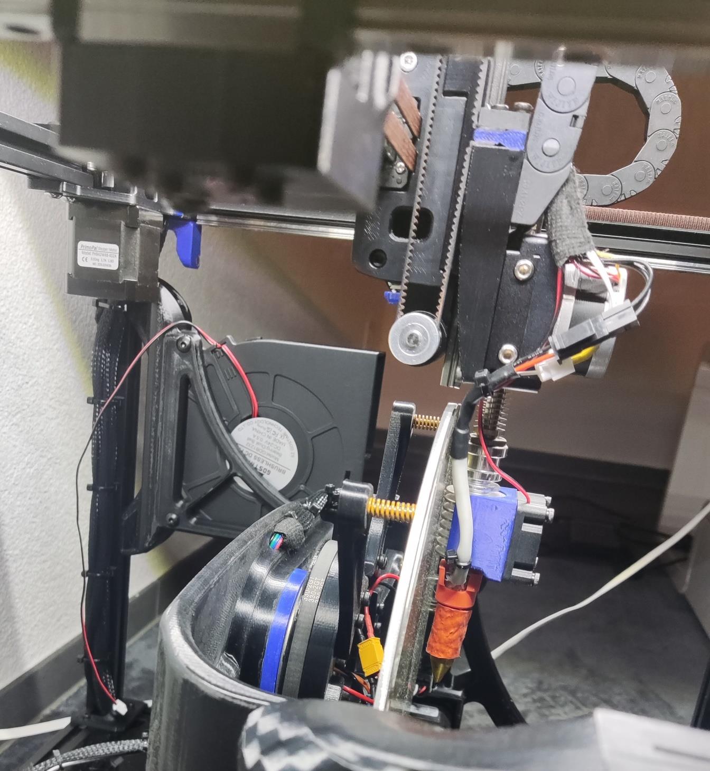
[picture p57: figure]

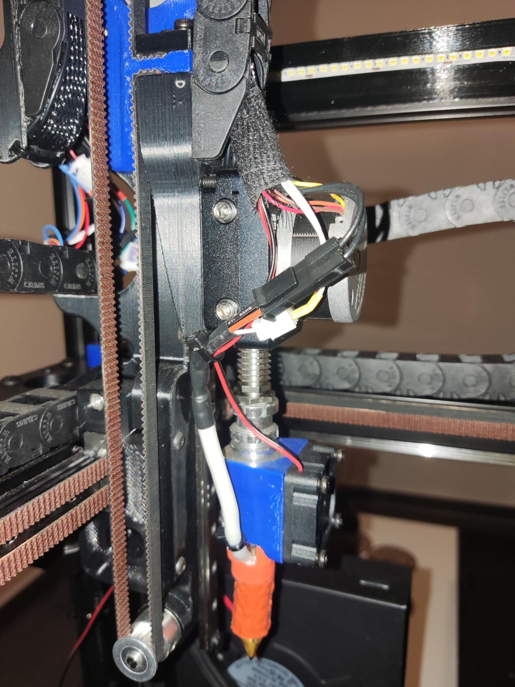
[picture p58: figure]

Also make connectors for the complete Z-axis so it can be easily removed or replaced.

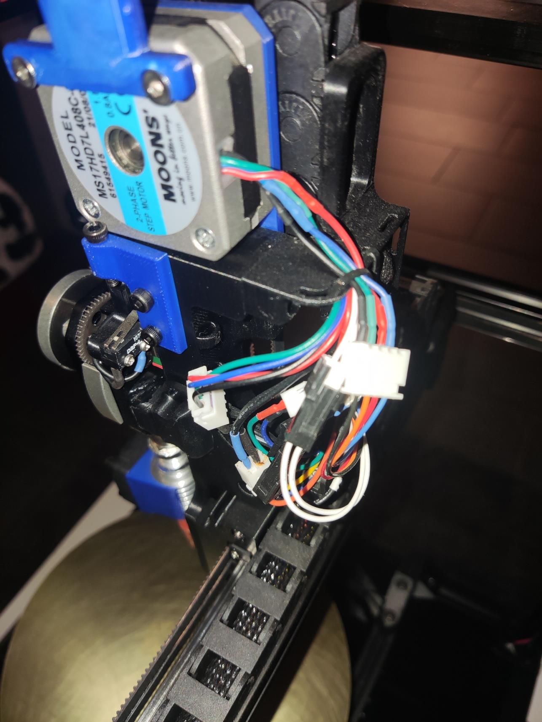
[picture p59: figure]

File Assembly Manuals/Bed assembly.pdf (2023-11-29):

# BED Assembly Manual for Voron Trident 250mm

Assembly manual for complete A and C axis bed with heated rotary PEI sheet

All 3D printed parts are designed to be printed from ABS filament . The optimal slicer settings for prints are:

Layer height: 0.2mm
Extrusion width: 0.4mm, forced
Infill pecentage: 50%
Infill type: gyroid, honeycomb, triangle, or cubic Wall count: 5
Solid top/bottom layers: 5

NO WARPING!

First assembly Aluminium extrusions, they have to be cutted exact lenghts specially the 180mm long ones.

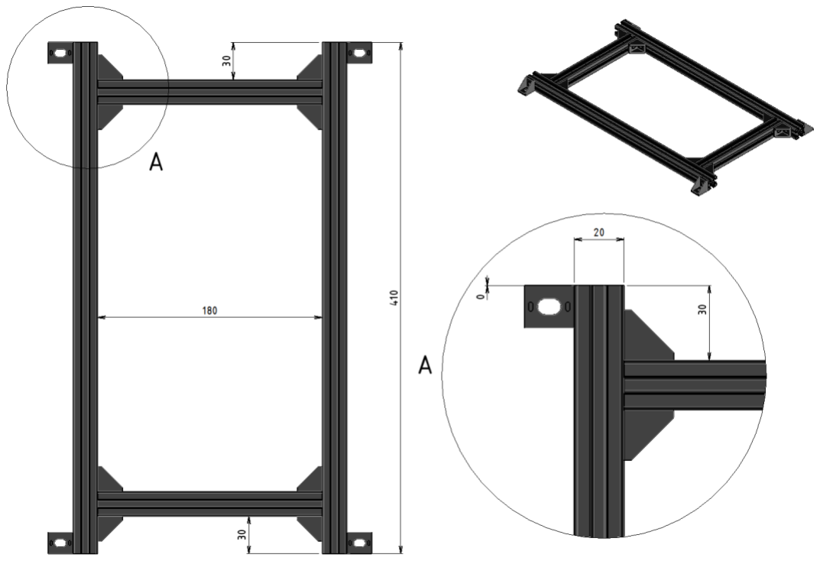
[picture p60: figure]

### Material used in this step :

Aluminium profile | 2x 180mm please | cut it to the tolerance +/- 0.03mm
| 2x 410mm | cut it to the tolerance +/- 0.05mm

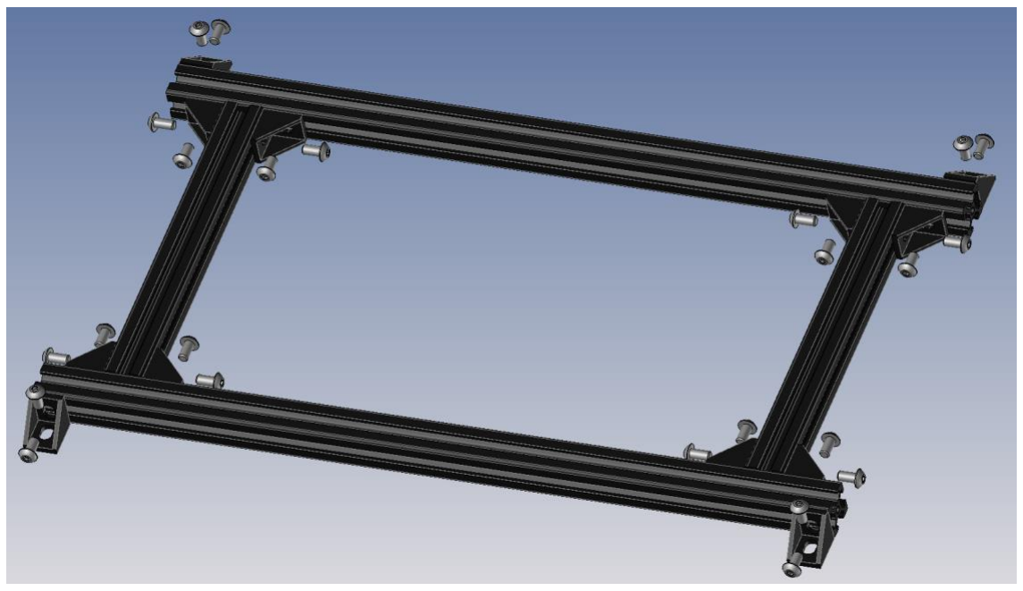
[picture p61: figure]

NOTE: Please make sure that you can assemble this step on maximum flat surface

The two 180 extrusions, must be maximally parallel and squared to the construction

Best if you have acces to the measuring device to control the distance

24x M5 x 10mm + T-nuts


NOTE: Please print this ABS part in high quality without any warping issues

The 8mm shaft should have, small tollerance H8 fit with the bearings 608zz


NOTE: Please print this ABS part in high quality without any warping issues

The 8mm shaft should have, small tollerance H8 fit with the bearings 608zz

6x M3 x 8mm

4x M3 washers

1x M8 washer


NOTE: Please do not tension the closed loop GT-2 belt 302 yet, leave it free so the motor and pulley can rotate easily

GT-2 Pulley 16T – 5mm bore

GT-2 Pulley 80T – 8mm bore

Closed loop GT-2 belt 6mm wide lenght 302 or 303 mm



NOTE: Please make sure the two ABS printed sides are squared with the base and also parallel

12x M5x20mm + Tnuts



NOTE: the heat inserts used, are M3 x 5mm



NOTE: the heat inserts used, are M3 x 7mm


NOTE: 3x M3x8mm + M3 washers

Slip ring dia Dia 22mm 4CH 10A

NOTE: 7x M3x8mm


NOTE: the heat inserts used, are M3 x 5mm


NOTE: | IGUS - PRT_04_30 Diameter 90mm
| 8x M3x10mm


NOTE: the pololu hub M3 threated holes, needs to be drilled out with 3.15 or 3.2 mm drill


NOTE: 4x M3x8mm + M3 washers


NOTE: GT-2 Pulley 20T

NOTE: 6x M3x20mm


NOTE: 2x M3x8mm + 1x M3x12mm, Closed loop GT-2 belt 6mm wide lenght 330 mm


NOTE: the heat inserts used, are M3 x 5mm


NOTE: 12x M3x8mm


NOTE: Please drill six holes into the magnetic sheet to match the aluminum hotbed

NOTE: 6x FHCS M3x22mm

Bed springs ID 3mm OD 6mm Lenght 15mm


NOTE: the adjustment with the bed springs for calibration of rotary bed will be done with Z axis on the printer


NOTE: now the tricky bit..

the lenght of swivel ABS parts is 280mm place the bed in between sides

and then push in the 8 mm shafts tighten up the right side and then the left side in mind,

the lenght in between M8 washers should be 280mm

Rotary bed should be swiveling freely on A axis and the sides shall not be bending when

the rotary is moving on A axis


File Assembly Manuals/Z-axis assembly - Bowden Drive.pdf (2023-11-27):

# Z- axis Assembly Manual for Voron Trident 250mm

Assembly manual for complete Z axis with Hotend and Extruder – BOWDEN DRIVE version

All 3D printed parts are designed to be printed from ABS filament . The optimal slicer settings for prints are:

Layer height: 0.2mm
Extrusion width: 0.4mm, forced
Infill pecentage: 50%
Infill type: gyroid, honeycomb, triangle, or cubic Wall count: 5
Solid top/bottom layers: 5

NO WARPING!


NOTE: the heat inserts used, are M2 x 4mm


NOTE: the heat inserts used, are M3 x 5mm



NOTE: Pulley GT-2 20T 5mm dia

Bearing 625 ZZ

Shaft 5mm, Lenght 45mm

Shaft collar ID 5mm

Spacer M5 x 1mm





NOTE: Screw M2 x 6mm

Linear Rail MGN7 – H 200mm ( use only hight quality Linear Rail )

Please secure the linear rail slider so will not fell out from the rail use rubber stoppers or

3D print them from printables

https://www.printables.com/model/347545-linear-rail-carriage-stop


NOTE: Screw M3 x 8mm and M3 x 16mm

neodymium magnets 6x3mm


NOTE: Screw M3 x 8mm

Pulley GT-2 20T 5mm dia


NOTE: Do not tight the tensions screws yet, so the stepper motor can slide


NOTE: heat inserts M3 x 5mm

Self taping Screw size M2

neodymium magnets 6x3mm

micro swicth

Please install magnets with polarity to hold hotend mechanisms holder on Z – axis to

Stop falling down when stepper motor is without power ( when printer is switched off )



NOTE: Screw M2 x 6mm

Spacer M2


NOTE: Please follow assembly from the Direct drive version of Z – axis for the GT-2 belt drive


NOTE: the heat inserts used, are M3 x 5mm



NOTE: Screw M2.5 x 6mm


NOTE: Pneumatic Coupler PC4-M10


NOTE: Screw FHSC M3 x 6mm for chain link 10x11

Screw SHCS M3 x 10mm for Hotend mounting

Chain link 10 x 11

The lenght of the chain link enough to to not interfere with upper stepper motor

mechanism when the extruder will reach max. bottom



NOTE: Screw SHCS M3 x 14 mm

24V Fan 30x30x10mm



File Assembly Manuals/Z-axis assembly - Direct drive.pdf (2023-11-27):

# Z- axis Assembly Manual for Voron Trident 250mm

Assembly manual for complete Z axis with Hotend and Extruder – DIRECT DRIVE version

All 3D printed parts are designed to be printed from ABS filament . The optimal slicer settings for prints are:

Layer height: 0.2mm
Extrusion width: 0.4mm, forced
Infill pecentage: 50%
Infill type: gyroid, honeycomb, triangle, or cubic Wall count: 5
Solid top/bottom layers: 5

NO WARPING!


NOTE: the heat inserts used, are M2 x 4mm


NOTE: the heat inserts used, are M3 x 5mm


NOTE: Pulley GT-2 20T 5mm dia

Bearing 625 ZZ

Shaft 5mm, Lenght 45mm

Shaft collar ID 5mm

Spacer M5 x 1mm




NOTE: Screw SHCS M2 x 6mm

Linear Rail MGN7 – H 200mm ( use only hight quality Linear Rail )

Please secure the linear rail slider so will not fell out from the rail use rubber stoppers or

3D print them from printables

https://www.printables.com/model/347545-linear-rail-carriage-stop


NOTE: Screw SHCS M3 x 8mm and SHCS M3 x 16mm

neodymium magnets 6x3mm


NOTE: Screw SHCS M3 x 8mm

Pulley GT-2 20T 5mm dia


NOTE: Do not tight the tensions screws yet, so the stepper motor can slide


NOTE: heat inserts M3 x 5mm

Self taping Screw size M2

neodymium magnets 6x3mm

micro swicth

Please install magnets with polarity to hold hotend mechanisms holder on Z – axis to

Stop falling down when stepper motor is without power ( when printer is switched off )



NOTE: Screw M2 x 6mm

Spacer M2


NOTE: Screw M3 x 10mm

Screw M3 x 16mm



NOTE: Screw M3 x 14mm

Belt GT-2

After assembling the belt, tension the stepper motor and tie-up the M3 screws


NOTE: Assembly the Hotend make the wires short with connectors

Later THE HOTEND can be swappable ! (for more see build pictures )


NOTE: Screw FHSC M3 x 22mm

Zip tie for filament PTFE tube


NOTE: heat inserts M3 x 5mm


NOTE: Screw M3 x 10mm



NOTE: Screw FHSC M3 x 6mm

Chain link 10 x 11

The lenght of the chain link enough to to not interfere with upper stepper motor

mechanism when the extruder will reach max. bottom


NOTE: Adapter from the extruder kit M6 to M10

Please use PTFE tube in between extruder and the Hotend 4mm OD, 2mm ID

Cut the lenght to the required size


NOTE: Screw SHSC M3 x 14mm

24V Fan 30x30x10mm


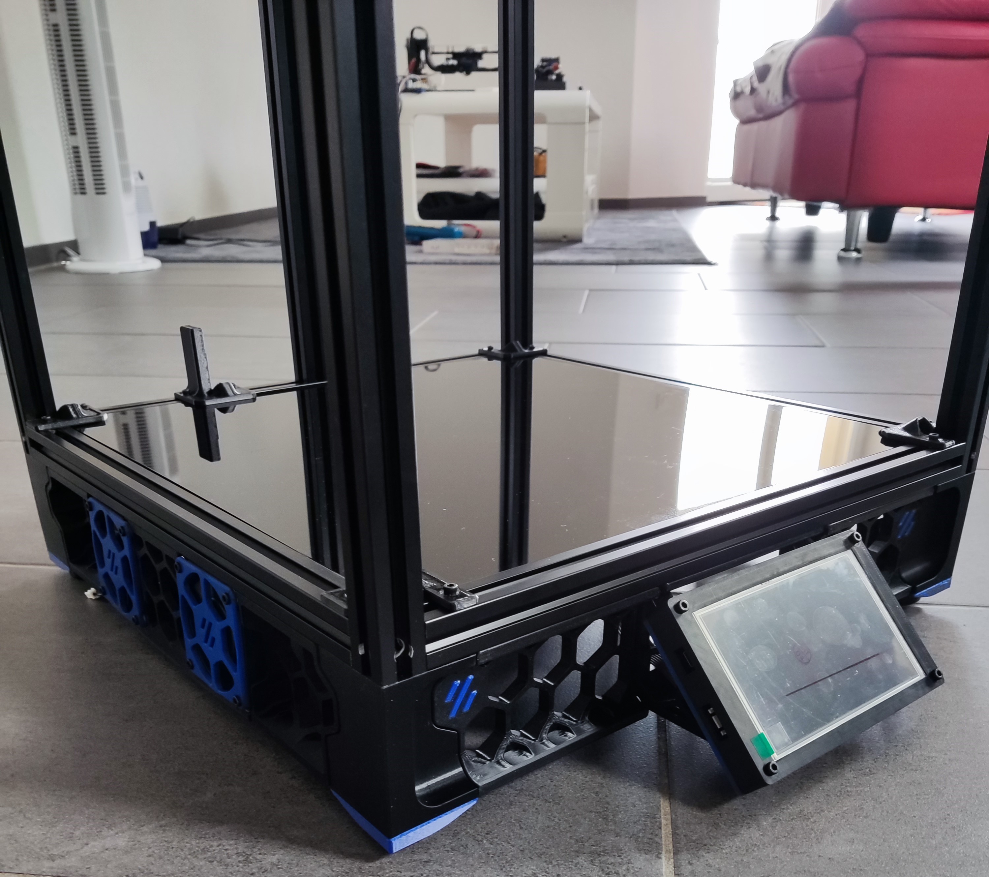
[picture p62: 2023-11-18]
Build Pictures/IMG_20230430_162640.jpg

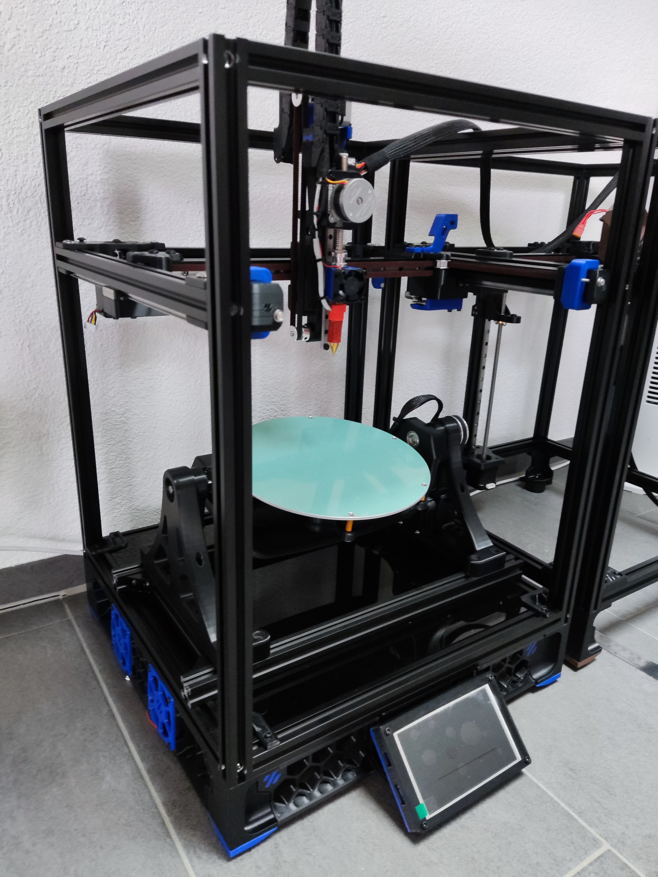
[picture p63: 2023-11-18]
Build Pictures/IMG_20230430_182625.jpg

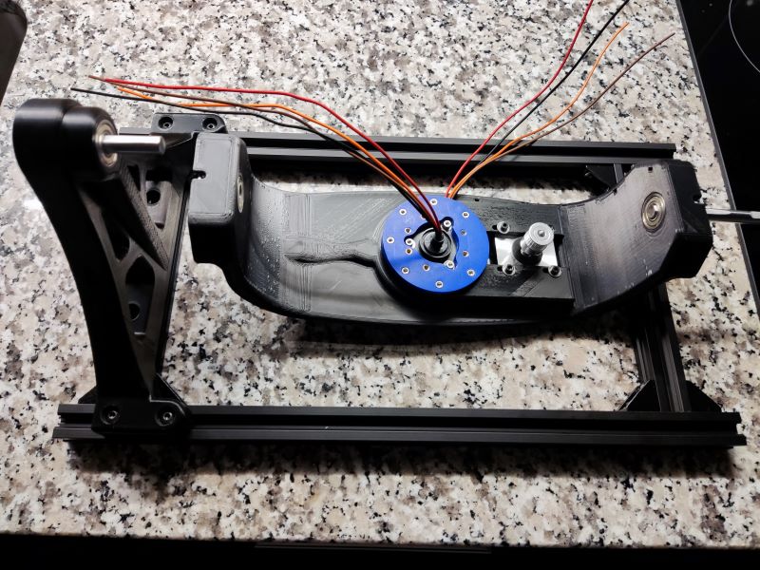
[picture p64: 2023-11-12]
Build Pictures/IMG_20230320_191843.jpg

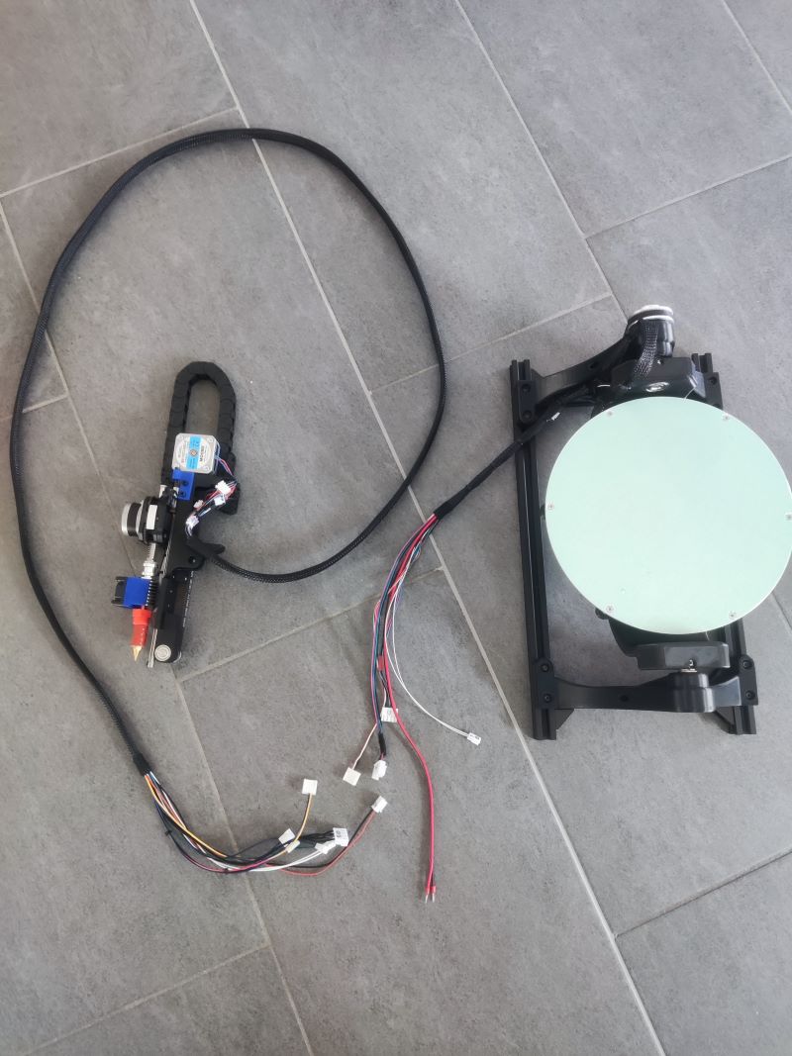
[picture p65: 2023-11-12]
Build Pictures/IMG_20230410_113114.jpg

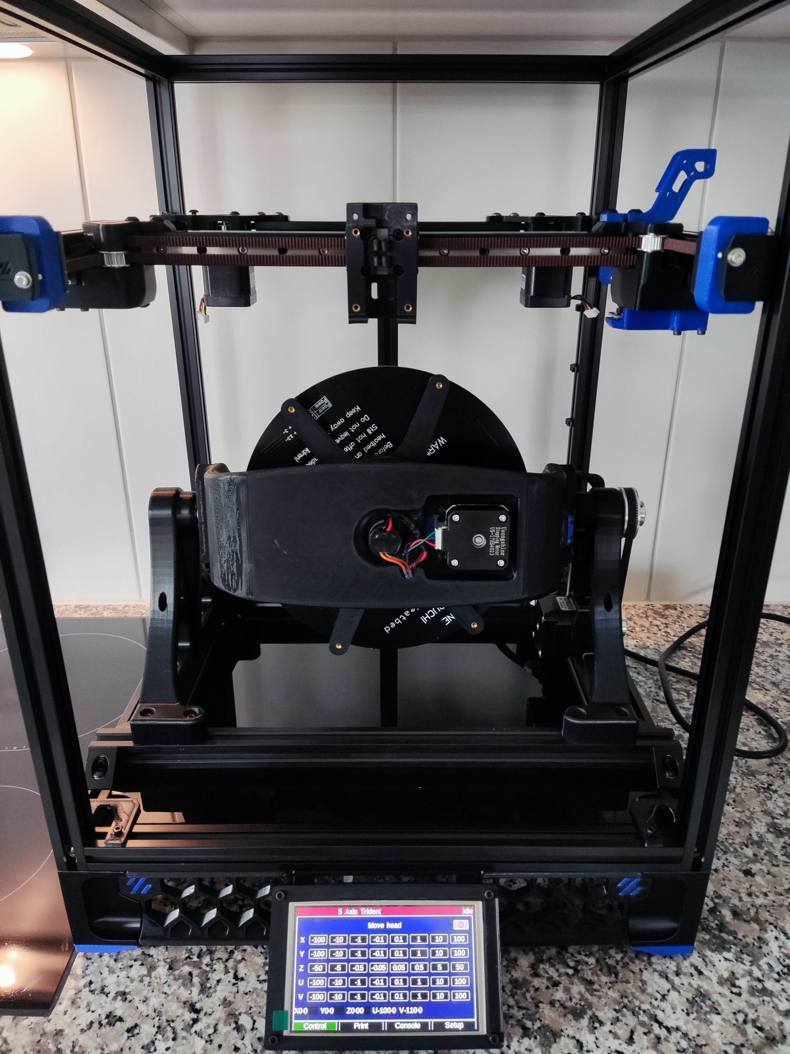
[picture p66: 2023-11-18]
Build Pictures/IMG_20230501_160411.jpg

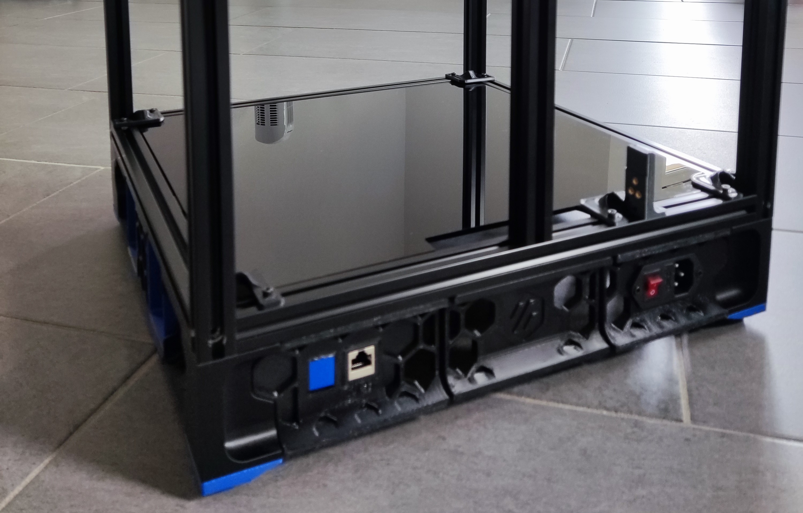
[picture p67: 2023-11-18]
Build Pictures/IMG_20230430_162713.jpg

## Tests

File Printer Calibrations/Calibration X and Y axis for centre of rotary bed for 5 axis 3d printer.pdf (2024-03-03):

# Calibration of X and Y axis for centre of rotary bed for 5-axis Voron Trident 3D printer modification

This is a guide with a g-code programme to calibrate the exact centre of the rotary bed for 5-axis 3D printers.

After assembling your printer and calibrating the Z axis to the correct print for print (Z=0.2mm) height and extruder calibration steps for the correct extrusion length.

Firstly, please print out the calibration g-code programme for your 5-axis 3D printer.

The program is designed to show any difference if the nozzle is not in the exact centre of the bed.

The printer must be set up in the exact centre of the rotary bed in order to use the 5-axis kinetics and to print the full 5-axis simultaneously.

In the first part of g-code program will print calibration strips exactly as show on the Figure 1a

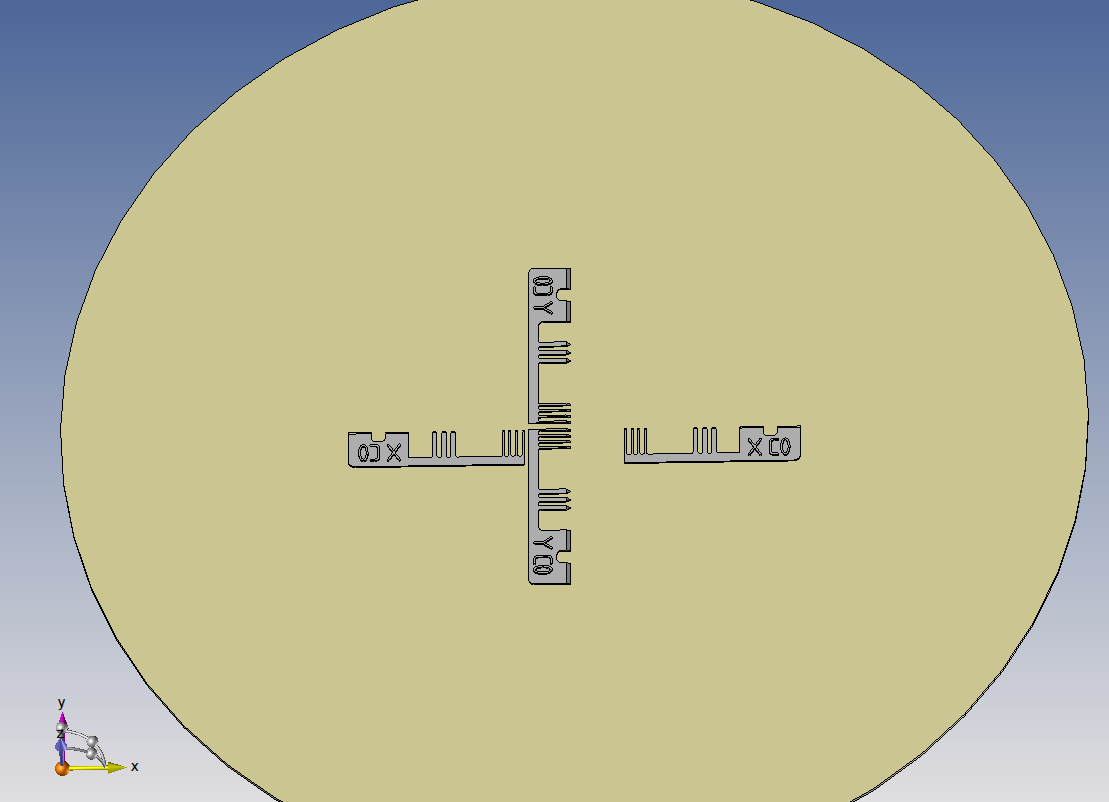
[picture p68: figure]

Figure 1a

The second part of the G-code programme will print exactly the same calibration strips, but after rotating the C-axis 180 degrees, so that when the print is complete and the nozzle is calibrated to the exact centre of the rotary bed, the full print should look like Figure 1b.

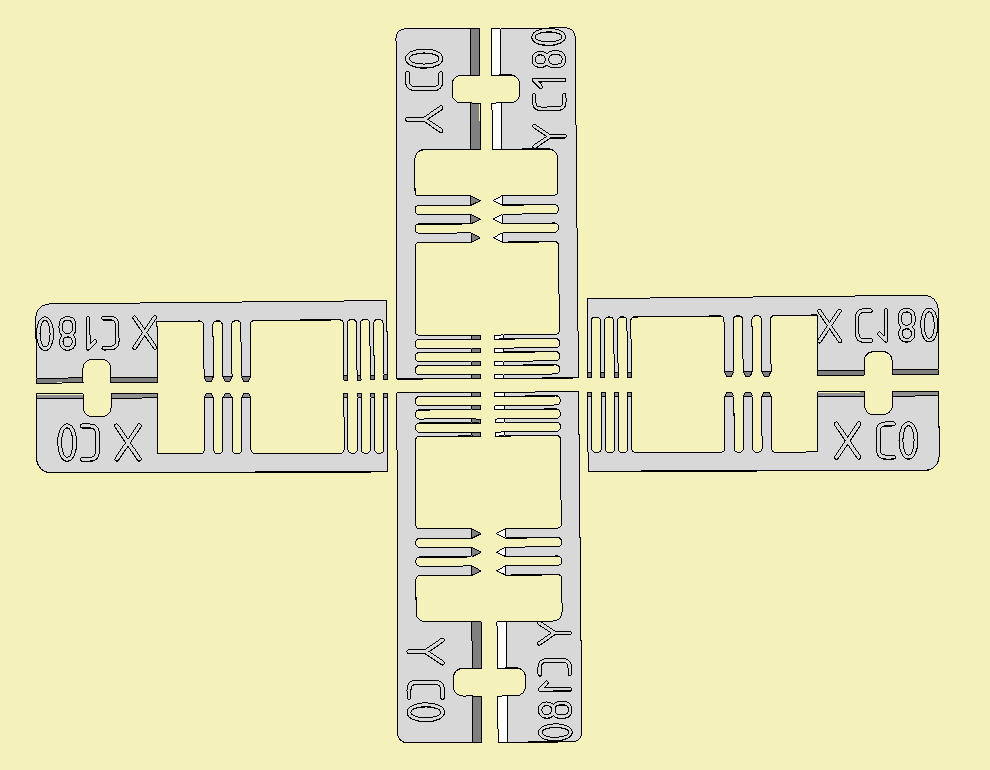
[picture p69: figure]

Figure 1b

As you can see, the calibration strips are aligned and there is no difference between the first printed

Calibration strip X C0 and the second printed calibration strip X C180 and the second printed calibration strip

Y C0 and calibration strip Y C180. This means that the nozzle is exactly in the centre of the rotary bed.

If the final print looks like Figure 2a, then the nozzle is not in the centre and adjustment is required to move the nozzle to the centre.

The adjustment is made in the printer settings in homex.g for the X axis and homey.g for the Y axis.

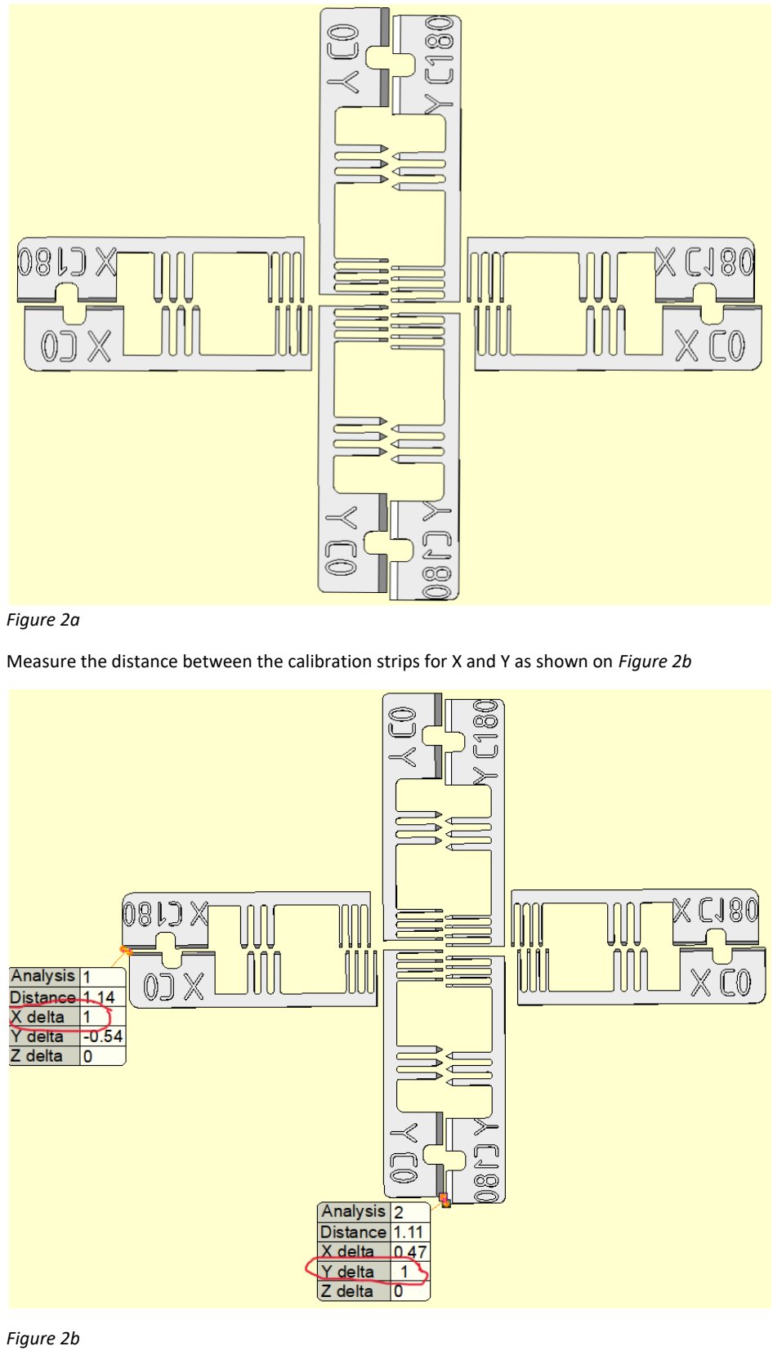
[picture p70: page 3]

Figure 2a

Measure the distance between the calibration strips for X and Y as shown on Figure 2b

Figure 2b

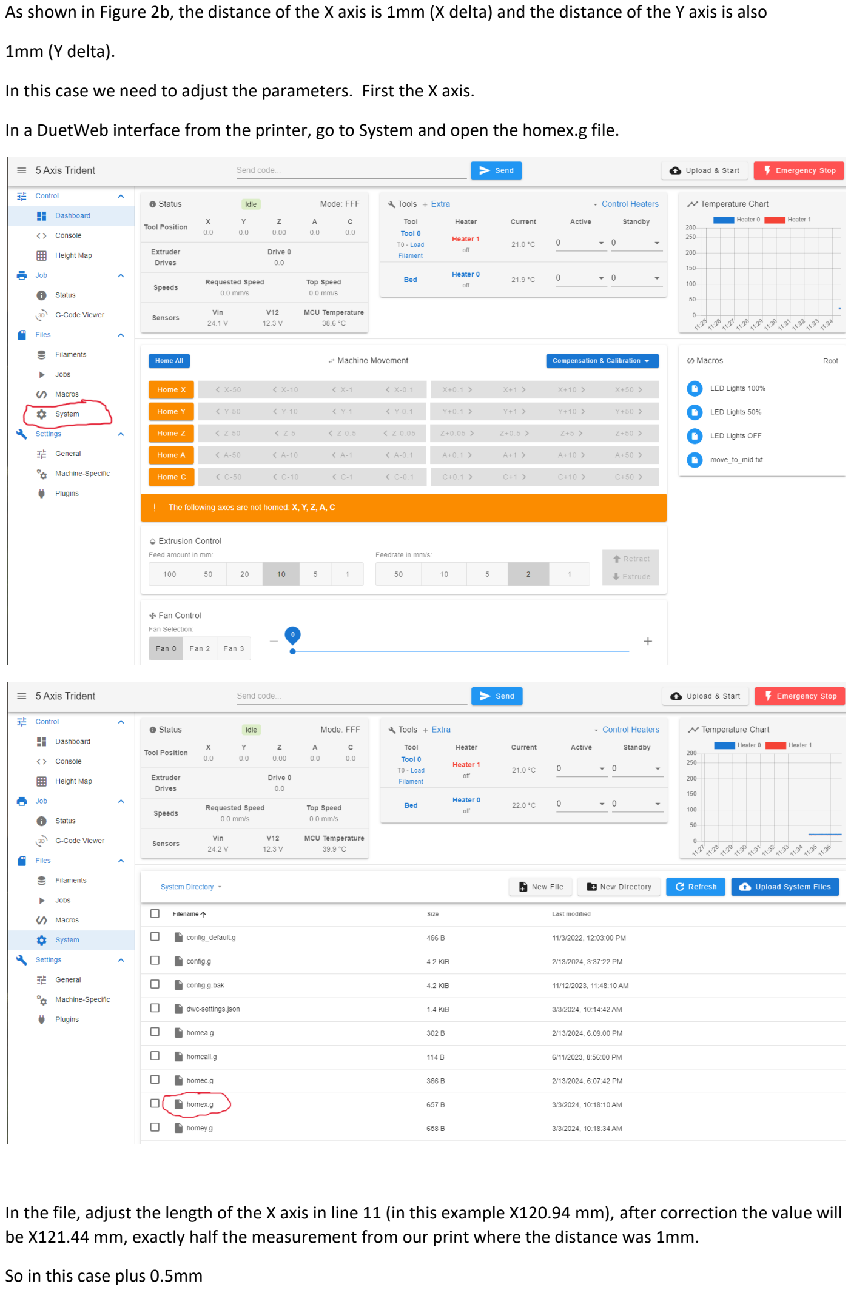
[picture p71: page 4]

As shown in Figure 2b, the distance of the X axis is 1mm (X delta) and the distance of the Y axis is also

1mm (Y delta).

In this case we need to adjust the parameters. First the X axis.

In a DuetWeb interface from the printer, go to System and open the homex.g file.

In the file, adjust the length of the X axis in line 11 (in this example X120.94 mm), after correction the value will be X121.44 mm, exactly half the measurement from our print where the distance was 1mm.

So in this case plus 0.5mm

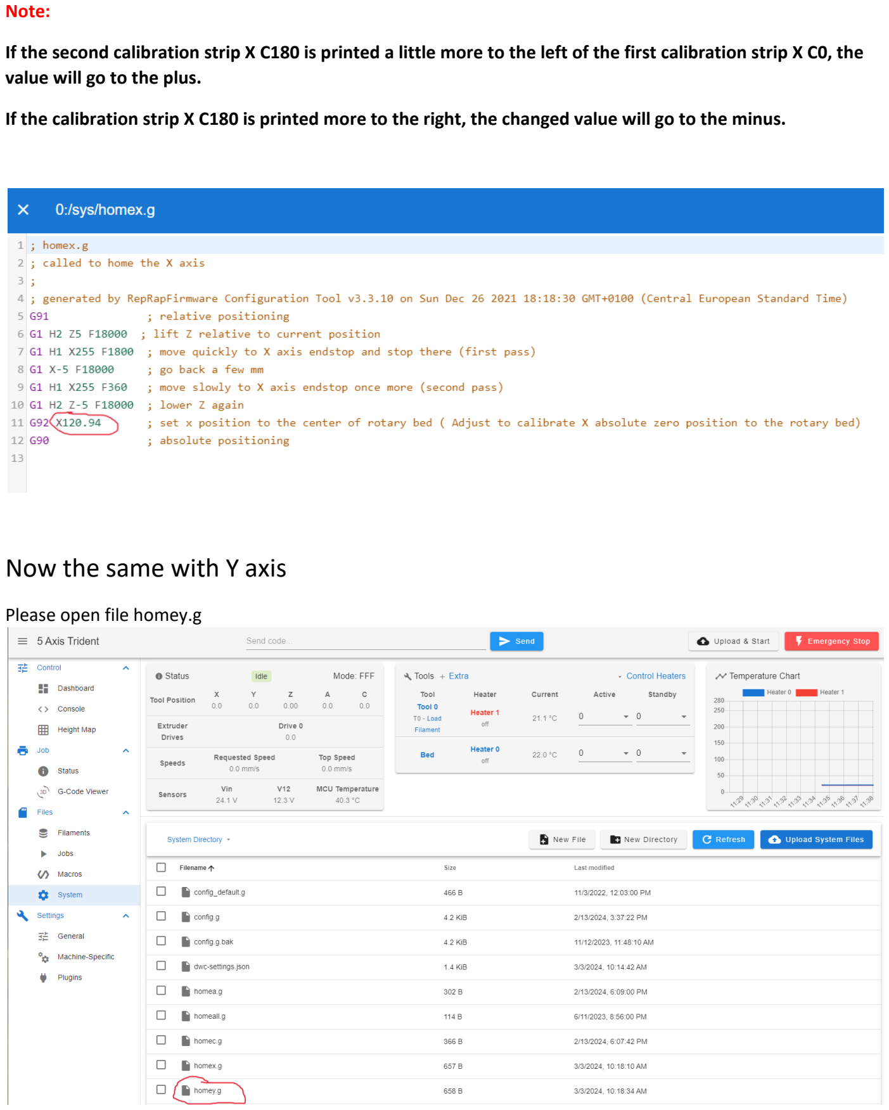
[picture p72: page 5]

Note:

If the second calibration strip X C180 is printed a little more to the left of the first calibration strip X C0, the value will go to the plus.

If the calibration strip X C180 is printed more to the right, the changed value will go to the minus.

## Now the same with Y axis

Please open file homey.g

In the file, adjust the length of the Y axis in line 11 (in this example Y107.74 mm), after correction the value will be Y108.24 mm, exactly half of the measurement from our print where the distance was 1mm.

So in this case plus 0.5mm

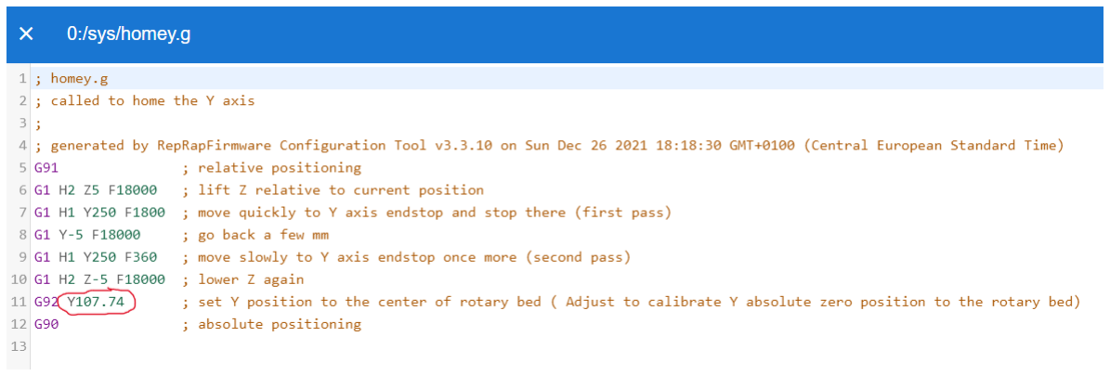
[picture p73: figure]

Note:

If the second calibration strip Y C180 is printed a little more to the upper of the first calibration strip Y C0, the value will go to the plus.

If the calibration strip Y C180 is printed more down, from Y C0 the changed value will go to the minus.

The printer should now be calibrated for absolute zero on the C axis of the rotary bed.

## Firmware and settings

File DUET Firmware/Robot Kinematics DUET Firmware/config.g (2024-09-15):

; Default config.g template for DuetPi
; Replace this with a proper configuration file (e.g from https://configtool.reprapfirmware.org)

; Display initial welcome message
;M291 P"Please go to <a href=""https://www.duet3d.com/StartHere"" target=""_blank"">this</a> page for further instructions on how to set it up." R"Welcome to your new Duet 3!" S1 T0

; Enable network
if {network.interfaces[0].type = "ethernet"}
    M552 P192.168.50.50 S1 ; P169.254.115.150 S1
else
    M552 S1
    
	
; Enable PanelDue
 M575 P1 S1 B57600


; General preferences
G90                                         ; Send absolute coordinates...
M83                                         ; ...but relative extruder moves
;M555 P2 									; Set firmware compatibility to look like Marlin

; set printer name
M550 P"5 Axis Trident"    

M669 K13 B"CoreXY5AC"
M669 A"X=0:120:0"
M669 A"Y=0:120:0"
M669 A"Z=0:120:0"
M669 A"A=-90:90:0"
M669 A"C=0"
M669 C"X=1:0:0:0:0:0"
M669 C"Y=0:1:0:0:0:0"
M669 C"Z=0:0:1:0:0:0"
M669 C"A=1:0:0:0:0:0"
M669 C"C=0:0:1:0:0:0"
M669 C"Mnoap=1:0:0:0:1:0:0:0:1:0:0:0"
M669 C"Mreference=0:0:0:0:0"
M669 S100
M669 T0.05

; Heaters BED
M308 S0 P"temp0" Y"thermistor" T100000 B3950 		; configure sensor 0 as thermistor on pin temp0
M950 H0 C"out0" T0                           		; create bed heater output on out0 and map it to sensor 0
M307 H0 R0.380 K0.410:0.000 D7.86 E1.35 S1.00 B0	; disable bang-bang mode for the bed heater and set PWM limit
M140 H0                                      		; map heated bed to heater 0
M143 H0 S120                                 		; set temperature limit for heater 0 to 120C


; Heaters HOTEND
M308 S1 P"temp1" Y"thermistor" T100000 B4725 C7.06e-8 ; configure sensor 1 as thermistor on pin temp1
M950 H1 C"out1" T1   						 ; create nozzle heater output on out1 and map it to sensor 1
M307 H1 R4.250 K1.828:0.000 D4.91 E1.35 S1.00 B0 V24.1  ; disable bang-bang mode for heater  and set PWM limit
M143 H1 S280                                 ; set temperature limit for heater 1 to 280C


; Drive Mappings
M569 P0 S1                                  ; Drive 1 goes forwards: X Axis
M569 P1 S1                                  ; Drive 1 goes forwards: Y Axis
M569 P2 S0                                  ; Drive 2 goes backwards: Z Axis
M569 P3 S0                                  ; Drive 3 goes backwards: E0
M569 P4 S0                                  ; Drive 4 goes anti-clockwise: A Axis
M569 P5 S1				    				; Drive 5 goes anti-clockwise: C Axis


M584 X0 Y1 Z2 E3 A4 C5 ; My Driver Mapping


;Microstepping and Speed

M350 X32 Y32 Z16 E16 A16 C16 I1                 			; Configure microstepping with interpolation

M92 X320.00 Y320.00 Z80.00 E720.0 A90.0 C68.885 		    ; Set steps per mm and steps per degree OLD VALUE E654.5
M566 X1200.00 Y1200.00 Z240.00 E270.00 A480.00 C480.00 P1     	    ; Set maximum instantaneous speed changes (mm/min)
M203 X3000.00 Y3000.00 Z2000.00 E2500.00 A2000.00 C6000.00  	    ; Set maximum speeds (mm/min)
M201 X1000.00 Y1000.00 Z1000.00 E1000.00 A1000.00 C1500.00   	    ; Set accelerations (mm/s^2)
M906 X650.00 Y650.00 Z650.00 E600.00 A2000.00 C600.00 I10            ; Set motor currents (mA) and motor idle factor in percent
M84 S3000                                    			    ; Set idle timeout


;Axis Limit
;Centre of the rotating bed is set to origin 0,0
;M208 X-110 Y-120 Z0 S1		;A-90 C-12000 S1 	; set axis minima
;M208 X125 Y109.5 Z127 S0 	;A90 C12000 S0 		; set axis maxima

;M564 H0								; allow unhomed movement


; Endstops
M574 X2 S1 P"!io1.in"
M574 Y2 S1 P"!io2.in"
M574 Z2 S1 P"io3.in"
M574 A1 S1 P"io4.in"
M574 C1 S3 

; Stallgaurd Sensitivy
M915 C S3 F0 H500 R1		                ; Set C axis Sensitivity


; Fans
M950 F0 C"out5" Q500                ; create fan 0 on pin out5 and set its frequency
M106 P0 S0 H-1                      ; set fan 0 value. Thermostatic control is
M950 F1 C"out7" Q500				; Creates HOTEND Fan
M106 P1 T45 S255 H1                 ; HOTEND Fan Settings
M950 F2 C"out8" Q500				; Creates CASE Fan 2
M106 P2  S55 H-1                 	; HOTEND Fan Settings
M950 F3 C"out9" Q500                ; create case fan 3 on pin out9 and set its frequency
M106 P3  S0 H-1                     ; set fan 3 value. Thermostatic control is turned ON
M950 F4 C"out6" Q500                ; create fan 4 on pin out6
M106 P4 S0 H-1                      ; set fan 4 value. 


; Tools
M563 P0 D0 H1 F0:4                                      ; define tool 0
G10 P0 X0 Y0 Z0                                       ; set tool 0 axis offsets
G10 P0 R0 S0                                          ; set initial tool 0 active and standby temperatures to 0C

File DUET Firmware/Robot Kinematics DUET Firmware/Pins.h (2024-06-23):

#ifndef PINS_H__
#define PINS_H__

// Load Pins_<platform>.h

#if !defined(PLATFORM)
# if defined(__SAM4E8E__)
#  define PLATFORM DuetNG
# elif defined(__SAME70Q20B__) || defined(__SAME70Q21B__) || defined(__SAMV71Q20B__)
#  if defined(DUET3_MB6HC)
#   define PLATFORM Duet3_MB6HC
#   define DUET3		1
#  elif defined(DUET3_MB6XD)
#   define PLATFORM Duet3_MB6XD
#   define DUET3		1
#  else
#   error Unknown platform
#  endif
# elif defined(DUET_M)
#  define PLATFORM DuetM
# elif defined(PCCB)
#  define PLATFORM Pccb
# elif defined(DUET3MINI_V04)
#  define DUET3MINI		1
#  define PLATFORM Duet3Mini
# elif defined(FMDC_V02) || defined(FMDC_V03)
#  define DUET3MINI		1
#  define PLATFORM FMDC
# else
#  error Unknown platform
# endif
#endif

#if !defined(P_INCLUDE_FILE)
# define P_EXPAND(x) x
# define P_CONCAT(x,y) P_EXPAND(x)y
# define P_STR(x) #x
# define P_XSTR(x) P_STR(x)
# define P_INCLUDE_FILE P_XSTR(P_CONCAT(Pins_,P_CONCAT(PLATFORM,.h)))
#endif

#include P_INCLUDE_FILE

// Apply default values to anything not configured
#ifndef SUPPORT_NONLINEAR_EXTRUSION
# define SUPPORT_NONLINEAR_EXTRUSION		1		// for now this is always enabled
#endif

#ifndef SUPPORT_WORKPLACE_COORDINATES
# define SUPPORT_WORKPLACE_COORDINATES		0
#endif

#ifndef SUPPORT_COORDINATE_ROTATION
# define SUPPORT_COORDINATE_ROTATION	SUPPORT_WORKPLACE_COORDINATES
#endif

#ifndef SUPPORT_LASER
# define SUPPORT_LASER			0
#endif

#ifndef SUPPORT_IOBITS
# define SUPPORT_IOBITS			0
#endif

#ifndef SUPPORT_12864_LCD
# define SUPPORT_12864_LCD		0
#endif

#ifndef SUPPORT_ILI9488_LCD
# define SUPPORT_ILI9488_LCD	0
#endif

#ifndef USE_FONT_CHIP
# define USE_FONT_CHIP		0
#endif

#define SUPPORT_DIRECT_LCD		(SUPPORT_12864_LCD || SUPPORT_ILI9488_LCD)
#define SUPPORT_ROTARY_ENCODER	SUPPORT_12864_LCD
#define SUPPORT_RESISTIVE_TOUCH	SUPPORT_ILI9488_LCD

#ifndef SUPPORT_LED_STRIPS
# define SUPPORT_LED_STRIPS		0
#endif

#ifndef SUPPORT_SPI_SENSORS
# define SUPPORT_SPI_SENSORS	1
#endif

#ifndef SUPPORT_BME280
# define SUPPORT_BME280			0
#endif

#define HAS_AUX_DEVICES			(defined(SERIAL_AUX_DEVICE))		// if SERIAL_AUX_DEVICE is defined then we have one or more aux devices

#ifndef SUPPORT_PANELDUE_FLASH
# define SUPPORT_PANELDUE_FLASH	HAS_AUX_DEVICES
#endif

#ifndef ALLOW_ARBITRARY_PANELDUE_PORT
# define ALLOW_ARBITRARY_PANELDUE_PORT (0)
#endif

#ifndef USE_CACHE
# define USE_CACHE				0
#endif

#ifndef USE_MPU
# define USE_MPU				0
#endif

#ifndef SUPPORT_TMC2660
# define SUPPORT_TMC2660		0
#endif

#ifndef SUPPORT_TMC22xx
# define SUPPORT_TMC22xx		0
#endif

#ifndef SUPPORT_TMC51xx
# define SUPPORT_TMC51xx		0
#endif

#ifndef VARIABLE_NUM_DRIVERS
# define VARIABLE_NUM_DRIVERS	0
#endif

#ifndef SUPPORT_CAN_EXPANSION
# define SUPPORT_CAN_EXPANSION	0
#endif

#ifndef DUAL_CAN
# define DUAL_CAN				0
#endif

#ifndef SUPPORT_OBJECT_MODEL
# define SUPPORT_OBJECT_MODEL	0
#endif

#define HAS_SMART_DRIVERS		(SUPPORT_TMC2660 || SUPPORT_TMC22xx || SUPPORT_TMC51xx)
#ifndef HAS_STALL_DETECT
# define HAS_STALL_DETECT		(SUPPORT_TMC2660 || SUPPORT_TMC51xx)
#endif

#ifndef SUPPORT_SLOW_DRIVERS
# define SUPPORT_SLOW_DRIVERS	1
#endif

#ifndef SUPPORT_BRAKE_PWM
# define SUPPORT_BRAKE_PWM		0
#endif

#ifndef HAS_12V_MONITOR
# define HAS_12V_MONITOR		0
# define ENFORCE_MIN_V12		0
#endif

#if !HAS_VOLTAGE_MONITOR
# define ENFORCE_MAX_VIN		0
#endif

// HAS_LWIP_NETWORKING refers to Lwip 2 support in the Networking folder, not legacy SAM3XA networking using Lwip 1
#ifndef HAS_LWIP_NETWORKING
# define HAS_LWIP_NETWORKING	0
#endif

#ifndef HAS_WIFI_NETWORKING
# define HAS_WIFI_NETWORKING	0
#endif

#if HAS_WIFI_NETWORKING && !defined(WIFI_USES_ESP32)
# define WIFI_USES_ESP32		0
#endif

#ifndef HAS_W5500_NETWORKING
# define HAS_W5500_NETWORKING	0
#endif

#ifndef HAS_RTOSPLUSTCP_NETWORKING
# define HAS_RTOSPLUSTCP_NETWORKING    0
#endif

#ifndef HAS_ESP32_NETWORKING
# define HAS_ESP32_NETWORKING    0
#endif

#define HAS_NETWORKING			(HAS_LWIP_NETWORKING || HAS_WIFI_NETWORKING || HAS_W5500_NETWORKING || HAS_RTOSPLUSTCP_NETWORKING || HAS_ESP32_NETWORKING)

#ifndef SUPPORT_HTTP
# define SUPPORT_HTTP			HAS_NETWORKING
#endif

#ifndef SUPPORT_FTP
# define SUPPORT_FTP			HAS_NETWORKING
#endif

#ifndef SUPPORT_TELNET
# define SUPPORT_TELNET			HAS_NETWORKING
#endif

#ifndef SUPPORT_MQTT
# define SUPPORT_MQTT			0
#endif

#ifndef SUPPORT_MULTICAST_DISCOVERY
# define SUPPORT_MULTICAST_DISCOVERY	0
#endif

#ifndef HAS_SBC_INTERFACE
# define HAS_SBC_INTERFACE		0
#endif

#ifndef HAS_MASS_STORAGE
# define HAS_MASS_STORAGE		1
#endif

#ifndef HAS_EMBEDDED_FILES
# define HAS_EMBEDDED_FILES		0
#endif

#if !HAS_MASS_STORAGE && !HAS_SBC_INTERFACE
# if SUPPORT_12864_LCD
#  error "12864 LCD support requires mass storage or SBC interface"
# endif
#endif

#if !HAS_MASS_STORAGE
# if SUPPORT_FTP
#  error "FTP support requires mass storage"
# endif
#endif

#ifndef SUPPORT_ASYNC_MOVES
# define SUPPORT_ASYNC_MOVES	0
#endif

#ifndef SUPPORT_KEEPOUT_ZONES
# define SUPPORT_KEEPOUT_ZONES	0
#endif
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

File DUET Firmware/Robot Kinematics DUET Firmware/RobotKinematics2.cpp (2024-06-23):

/*
 * RobotKinematics2.cpp
 *
 *  Created on: 06 Aug 2023
 *      Author: JoergS5
 */

#include <Movement/Kinematics/RobotKinematics.h>

#if SUPPORT_ROBOT

/*
 * angles is in degrees (rotary axis) or mm (linear axis)
 * angles are sorted by chain, i.e. CAZXY
 */

void RobotKinematics::getForwardBySkew(const float *angles, float *mxTo) const noexcept {
	for(int i=0; i < numOfAxes; i++) {
		if(axisTypes[i] == 'R') {
			int rotarynr = getRotaryIndex(i);
			getRodrigues2_Rot(&cache[i*3 + offsetScrewOmega], &cache[i*3+ offsetScrewQ],
					&cache[rotarynr*12 + offsetScrewOmega2], &cache[rotarynr*3 + offsetScrewV],
					(angles[i] - cache[offsetMreference+i]) / radiansToDegrees, mxTemp);
		}
		else {
			getRodrigues2_Pris(&cache[i*3+ offsetScrewOmega], angles[i] - cache[offsetMreference+i], mxTemp);
		}
		if(i == 0) {
			memcpy(mxTo, mxTemp, sizeof(float) * 12);
		}
		else {
			multiplyRotationMatrixInplaceLeft(mxTo, mxTemp);
		}
	}
	multiplyRotationMatrixInplaceLeft(mxTo, screw_M);
}

void RobotKinematics::getRodrigues2_Pris(float *screwOmega, float dist, float *_mxTemp) const noexcept {
	_mxTemp[0] = 1.0;
	_mxTemp[4] = 0.0;
	_mxTemp[8] = 0.0;
	_mxTemp[1] = 0.0;
	_mxTemp[5] = 1.0;
	_mxTemp[9] = 0.0;
	_mxTemp[2] = 0.0;
	_mxTemp[6] = 0.0;
	_mxTemp[10] = 1.0;

	_mxTemp[3] = screwOmega[0] * dist;
	_mxTemp[7] = screwOmega[1] * dist;
	_mxTemp[11] = screwOmega[2] * dist;

}

/*
 * create transformation matrix based on exponential screw/skew values
 * version without using cache
 *
 * \param screw 6 parameters: 3 skew, 3 q positions on axis
 *
 * \param theta in radians
 *
 * \param T resulting transformation matrix 3x4
 */

void RobotKinematics::getRodrigues(float *screwO, float *screwQ, float theta,
		float *mx, bool isRotational) const noexcept {
	if(isRotational) {
		float v[3], omega2[9];
		setRodrigues1(screwO, screwQ, omega2, v);
		getRodrigues2_Rot(screwO, screwQ, omega2, v, theta, mx);
	}
	else {
		getRodrigues2_Pris(screwO, theta, mx);
	}
}

/*
 * prepare Rodrigues part 1, the parts which do not depend on theta
 *
 * the result is cached:
 * v is the cross product of w and q
 * omega2 is omega squared, a 3x3 matrix
 */

void RobotKinematics::setRodrigues1(float *screwO, float *screwQ, float *omega2, float *v) const noexcept {
	// v = - w x q
	v[0] = -screwO[1]*screwQ[2] + screwO[2]*screwQ[1];
	v[1] = -screwO[2]*screwQ[0] + screwO[0]*screwQ[2];
	v[2] = -screwO[0]*screwQ[1] + screwO[1]*screwQ[0];

	float omega[9];
	omega[0] = 0.0;
	omega[4] = 0.0;
	omega[8] = 0.0;

	omega[1] = - screwO[2];
	omega[2] = screwO[1];
	omega[3] = screwO[2];
	omega[5] = - screwO[0];
	omega[6] = - screwO[1];
	omega[7] = screwO[0];

	multiplyMatrix(3, 3, omega, 3, omega, omega2);
}

/*
 * Rodrigues part 2, calculating T from known properties and theta
 */

void RobotKinematics::getRodrigues2_Rot(const float *screwO, const float *screwQ_notused, const float *omega2,
		const float *v, float theta, float *mx) const noexcept {
	float sinTheta = 0.0, oneMinCos = 0.0, thetaMinSinTheta = 0.0;
	if(theta != 0.0) {
		sinTheta = sinf(theta);
		oneMinCos = 1.0f - cosf(theta);
		thetaMinSinTheta = theta - sinTheta;
	}

	// calculate rotations:
	mx[0] = 1.0f + oneMinCos * omega2[0];
	mx[1] = sinTheta * (- screwO[2]) + oneMinCos * omega2[1];
	mx[2] = sinTheta * screwO[1] + oneMinCos * omega2[2];

	mx[4] = sinTheta * screwO[2] + oneMinCos * omega2[3];
	mx[5] = 1.0f + oneMinCos * omega2[4];
	mx[6] = sinTheta * (- screwO[0]) + oneMinCos * omega2[5];

	mx[8] = sinTheta * (- screwO[1]) + oneMinCos * omega2[6];
	mx[9] = sinTheta * screwO[0] + oneMinCos * omega2[7];
	mx[10] = 1.0f + oneMinCos * omega2[8];

	// calculate positions: Lynch/Park page 105, alternative method see Murray/Li/Sastry page 42
	// Pardos-Gotor page 42
	mx[3] = (thetaMinSinTheta * omega2[0] + theta) * v[0] +
			(oneMinCos * (- screwO[2]) + thetaMinSinTheta * omega2[1]) *  v[1] +
			(oneMinCos * screwO[1] + thetaMinSinTheta * omega2[2])  * v[2];
	mx[7] = (oneMinCos * screwO[2] + thetaMinSinTheta * omega2[3]) * v[0] +
			(thetaMinSinTheta * omega2[4] + theta) *  v[1] +
			(oneMinCos * (- screwO[0]) + thetaMinSinTheta * omega2[5])  * v[2];
	mx[11] = (oneMinCos * (- screwO[1]) + thetaMinSinTheta * omega2[6]) * v[0] +
			(oneMinCos * screwO[0] + thetaMinSinTheta * omega2[7]) *  v[1] +
			(thetaMinSinTheta * omega2[8] + theta)  * v[2];
}

/* store Mnoap and its inverse
 *
 * Mnaop is the endpoint for given actuator angles/positions and default tool length/orientation
 *
 * \param values: x-axis, y-axis, z-axis, pos values as 3-value vectors each, in this order
 *
 */

void RobotKinematics::setSkew_M(float *values) const noexcept {
	screw_M[0] = values[0];
	screw_M[4] = values[1];
	screw_M[8] = values[2];

	screw_M[1] = values[3];
	screw_M[5] = values[4];
	screw_M[9] = values[5];

	screw_M[2] = values[6];
	screw_M[6] = values[7];
	screw_M[10] = values[8];

	screw_M[3] = values[9];
	screw_M[7] = values[10];
	screw_M[11] = values[11];

	normalizeVector(screw_M[0], screw_M[4], screw_M[8]);
	normalizeVector(screw_M[1], screw_M[5], screw_M[9]);
	normalizeVector(screw_M[2], screw_M[6], screw_M[10]);

	recalcMInv();
}

void RobotKinematics::recalcMInv() const noexcept {
	//MT
	screw_MInv[0] = screw_M[0];	screw_MInv[4] = screw_M[1];	screw_MInv[8] = screw_M[2];
	screw_MInv[1] = screw_M[4];	screw_MInv[5] = screw_M[5];	screw_MInv[9] = screw_M[6];
	screw_MInv[2] = screw_M[8];	screw_MInv[6] = screw_M[9];	screw_MInv[10] = screw_M[10];
	//-MT*t
	screw_MInv[3] = -(screw_MInv[0]*screw_M[3] + screw_MInv[1]*screw_M[7] + screw_MInv[2]*screw_M[11]);
	screw_MInv[7] = -(screw_MInv[4]*screw_M[3] + screw_MInv[5]*screw_M[7] + screw_MInv[6]*screw_M[11]);
	screw_MInv[11] = -(screw_MInv[8]*screw_M[3] + screw_MInv[9]*screw_M[7] + screw_MInv[10]*screw_M[11]);
}

int RobotKinematics::getRotaryIndex(int axisnr) const noexcept {
	int ct = 0;
	for(int i=0; i < numOfAxes; i++) {
		if(axisTypes[i] == 'R') {
			if(i == axisnr) {
				return ct;
			}
			ct++;
		}
	}
	return -1; // not found or axisnr wrong
}

/*
 * multiply two matrices
 *
 * \param m, r, n rows first, cols first (== rows second), cols second
 * \param mx1 first matrix in format m x r
 * \param mx2 second matrix in format r x n
 * \param mxTo result in format m x n
 *
 * cost: m*n*r(A,M) (m*n*r additions and m*n*r multiplications), T would be for trigonometric
 */

void RobotKinematics::multiplyMatrix(int m, int r, const float *mx1, int n, const float *mx2, float *mxTo) const noexcept {
	for(int row = 0; row < m; row++) {
		for(int col = 0; col < n; col++) {
			mxTo[row * n + col] = 0.0f;
			for(int e = 0; e < r; e++) {
				mxTo[row * n + col] += mx1[row * r + e] * mx2[e * n + col];
			}
		}
	}
}
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

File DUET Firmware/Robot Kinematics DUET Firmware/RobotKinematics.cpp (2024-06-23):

/*
 * RobotKinematics.cpp
 *
 *  Created on: 06 Aug 2023
 *      Author: JoergS5
 */


#include <Movement/Kinematics/RobotKinematics.h>
#include <GCodes/GCodeBuffer/GCodeBuffer.h>
#include <Platform/RepRap.h>
#include <Movement/DDA.h>

#if SUPPORT_OBJECT_MODEL

// Object model table and functions
// Note: if using GCC version 7.3.1 20180622 and lambda functions are used in this table, you must compile this file with option -std=gnu++17.
// Otherwise the table will be allocated in RAM instead of flash, which wastes too much RAM.

// Macro to build a standard lambda function that includes the necessary type conversions
#define OBJECT_MODEL_FUNC(...) OBJECT_MODEL_FUNC_BODY(RobotKinematics, __VA_ARGS__)

constexpr ObjectModelTableEntry RobotKinematics::objectModelTable[] =
{
	// Within each group, these entries must be in alphabetical order
	// 0. kinematics members
	{ "name",	OBJECT_MODEL_FUNC(self->GetName(true)), 	ObjectModelEntryFlags::none },
	//TODO lots more to be added here
};

constexpr uint8_t RobotKinematics::objectModelTableDescriptor[] = { 1, 1 };

DEFINE_GET_OBJECT_MODEL_TABLE_WITH_PARENT(RobotKinematics, ZLeadscrewKinematics)

#endif


RobotKinematics::RobotKinematics() noexcept
	: ZLeadscrewKinematics(KinematicsType::scara, SegmentationType(true, false, false))
{
}

RobotKinematics::~RobotKinematics() {
}

const char *RobotKinematics::GetName(bool forStatusReport) const noexcept {
	return "robot";
}

bool RobotKinematics::Configure(unsigned int mCode, GCodeBuffer& gb, const StringRef& reply,
		bool& error) THROWS(GCodeException) {

	if (mCode == 669)
	{
		bool seen = false;
		bool allowEmpty = false;
		bool letterUsed = false;

		if (gb.Seen('B')) {
			gb.TryGetQuotedString('B', tempS50.GetRef(), seen, allowEmpty);
			setB(tempS50.c_str());
			seen = true; // => unhome
			letterUsed = true;
		}

		if (gb.Seen('A')) {
			gb.TryGetQuotedString('A', tempS50.GetRef(), seen, allowEmpty);
			setA(tempS50.c_str());
			seen = true; // => unhome
			letterUsed = true;
		}

		if (gb.Seen('P')) {
			gb.TryGetQuotedString('P', tempS50.GetRef(), seen, allowEmpty);
			setP(tempS50.c_str());
			seen = true; // => unhome
			letterUsed = true;
		}

		if (gb.Seen('C')) {
			gb.TryGetQuotedString('C', tempS50.GetRef(), seen, allowEmpty);
			setC(tempS50.c_str());
			seen = true; // => unhome
			letterUsed = true;
		}

		if (gb.Seen('R')) {
			float avgTime = sumOfTimes / (float) timeMeasurements;
			tempS50.Clear();
			tempS50.catf("avg Time inverse kin: %.2f microseconds", (double) avgTime);
			consoleMessage(tempS50.GetRef());
			tempS50.copy("\n");
			consoleMessage(tempS50.GetRef());
			sumOfTimes = 0;
			timeMeasurements = 0;
			letterUsed = true;
		}

		// set not to unhome
		if (gb.Seen('D')) {
			seen = false; // don't unhome
			letterUsed = true;
		}

		if(!letterUsed) {
			reportConfiguration(gb);
		}

		return seen;
	}
	else
	{
		return ZLeadscrewKinematics::Configure(mCode, gb, reply, error);
	}
}

bool RobotKinematics::CartesianToMotorSteps(const float machinePos[], const float stepsPerMm[],
		size_t numVisibleAxes, size_t numTotalAxes, int32_t motorPos[], bool isCoordinated) const noexcept {


	if(specialMethod == 1) { // CoreXY
		int i = -1;
		bool isAC = true;
		if(abcType == 0) {
			i = getPositionOfLetterInChain('A');
			isAC = true;
		}
		else if(abcType == 1) {
			i = getPositionOfLetterInChain('B');
			isAC = false;
		}
		const float ABpt[3] = { cache[i*3+ offsetScrewQ], cache[i*3+ offsetScrewQ+1], cache[i*3+ offsetScrewQ+2]};
		i = getPositionOfLetterInChain('C');
		const float Cpt[3] = { cache[i*3+ offsetScrewQ], cache[i*3+ offsetScrewQ+1], cache[i*3+ offsetScrewQ+2]};

		float result[5];
		GACartesianToMotor(machinePos, ABpt, Cpt, result, isAC);

		float coreX = result[0];
		float coreY = result[1];
		if(specialMethod == 1) { // CoreXY
			coreX = result[0] + result[1];
			coreY = result[0] - result[1];
		}
		motorPos[0] = lrintf(coreX * stepsPerMm[0]); // X (A stepper)
		motorPos[1] = lrintf(coreY * stepsPerMm[1]); // Y (B stepper)
		motorPos[2] = lrintf(result[2] * stepsPerMm[2]); // Z
		motorPos[3] = lrintf(machinePos[3] * stepsPerMm[3]); // A/B
		motorPos[4] = lrintf(machinePos[4] * stepsPerMm[4]); // C
	}

	for (size_t axis = numOfAxes; axis < numVisibleAxes; ++axis)	{
		motorPos[axis] = lrintf(machinePos[axis] * stepsPerMm[axis]);
	}


	return true;
}

//called after connection established, called once for every segment move:

void RobotKinematics::MotorStepsToCartesian(const int32_t motorPos[], const float stepsPerMm[],
		size_t numVisibleAxes, size_t numTotalAxes, float machinePos[]) const noexcept {
	startClock();

	if(specialMethod == 1) { // CoreXY
		float angles[numOfAxes];
		if(specialMethod == 1) { // CoreXY
			angles[0] = 0.5*((float) motorPos[0] / stepsPerMm[0] + (float) motorPos[1] / stepsPerMm[1]);
			angles[1] = 0.5*((float) motorPos[0] / stepsPerMm[0] - (float) motorPos[1] / stepsPerMm[1]);
		}
		else {
			angles[0] = (float) motorPos[0] / stepsPerMm[0]; // X
			angles[1] = (float) motorPos[1] / stepsPerMm[1]; // Y
		}
		angles[2] = (float) motorPos[2] / stepsPerMm[2]; // Z
		angles[3] = (float) motorPos[3] / stepsPerMm[3]; // A or B
		angles[4] = (float) motorPos[4] / stepsPerMm[4]; // C

		int i = -1;
		bool isAC = true;
		if(abcType == 0) {
			i = getPositionOfLetterInChain('A');
			isAC = true;
		}
		else if(abcType == 1) {
			i = getPositionOfLetterInChain('B');
			isAC = false;
		}
		const float ABpt[3] = { cache[i*3+ offsetScrewQ], cache[i*3+ offsetScrewQ+1], cache[i*3+ offsetScrewQ+2]};
		i = getPositionOfLetterInChain('C');
		const float Cpt[3] = { cache[i*3+ offsetScrewQ], cache[i*3+ offsetScrewQ+1], cache[i*3+ offsetScrewQ+2]};

		GAMotorToCartesian(angles, ABpt, Cpt, machinePos, isAC);
	}

	sumOfTimes += stopClock();
	timeMeasurements++;

}

bool RobotKinematics::IsReachable(float axesCoords[MaxAxes], AxesBitmap axes) const noexcept {
	return true;
}

LimitPositionResult RobotKinematics::LimitPosition(float coords[], const float * null initialCoords,
		size_t numVisibleAxes, AxesBitmap axesToLimit, bool isCoordinated, bool applyM208Limits) const noexcept {

//	const bool m208Limited = applyM208Limits && Kinematics::LimitPositionFromAxis(coords, 0, numVisibleAxes, axesToLimit);
//	return (m208Limited) ? LimitPositionResult::adjusted : LimitPositionResult::ok;

	return LimitPositionResult::ok;
}

void RobotKinematics::GetAssumedInitialPosition(size_t numAxes, float positions[]) const noexcept {

}

AxesBitmap RobotKinematics::AxesAssumedHomed(AxesBitmap g92Axes) const noexcept {
	return g92Axes;
}

AxesBitmap RobotKinematics::MustBeHomedAxes(AxesBitmap axesMoving, bool disallowMovesBeforeHoming) const noexcept {
	return axesMoving;
}
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

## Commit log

2023-11-18 z axis stl
    [Belt tensioner Bottom.stl, Belt tensioner.stl, Cooling Fan Holder.stl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]
2023-11-18 repairing files
    [Belt tensioner Bottom.stl, Belt tensioner Top.stl]
2023-11-18 Update Parts List - Trident 5 axis.xlsx
    [Parts List - Trident 5 axis.xlsx]
2023-11-19 Update Trident 5 axis assembly.pdf
2023-11-20 wiring guide
    [DUET_6HC_wiring.xlsx]
2023-11-26 Update to Direct drive version
    [10x11-chain-edge1.stl, 10x11-chain-edge2.stl, Extruder_linerar_rail_mount.stl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]
2023-11-27 bowden drive z axis stl
    [Extruder_linerar_rail_mount.stl, indicator clock holder - Bowden drive.stl]
2023-11-27 Update
    There are now two versions for the Z-axis mechanism. Direct drive with OMG extruder and V6 hotend and Bowden Drive with Phaetus hotend and BMG extruder.
    Part list is updated as well to match the required components
    [Parts List - Trident 5 axis.xlsx]
2024-03-03 Calibration X and Y axis
2024-03-03 Printer Calibrations
2024-06-23 Change of Firmware for 5 axis
    Two versions are available the first is based on standard DUET firmware and the 5 axis are mechanically set for the centre of rotary bed.
    The second is still in TEST PHASE! its full 5 axis robot kinematics DUET Firmware
    [config.g, config_default.g, homeRobot.g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]
2024-09-15 Updates for extra part cooling Fan and bed centring screws
    I have updated the printer and assembly manuals. I have issues with part cooling when printing in higher speeds so there is now installed second auxiliary fan on right side and new part fan blowers.
    Also new design for bed centring screws now the rotary bed can be adjustable from bottom with screws.
    [DUET_6HC_wiring.xlsx, Parts List - Trident 5 axis.xlsx, Robot Kinematics testing pin.stl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]
2024-10-07 Update Bed assembly.pdf
